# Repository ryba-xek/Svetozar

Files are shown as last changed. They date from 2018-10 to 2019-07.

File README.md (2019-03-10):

# Svetozar: an open-source e-vehicles peripherals controller

View this project on [CADLAB.io](https://cadlab.io/project/1290).

_Current project status_: in active development. Some features work, some don't.

## In a nutshell:

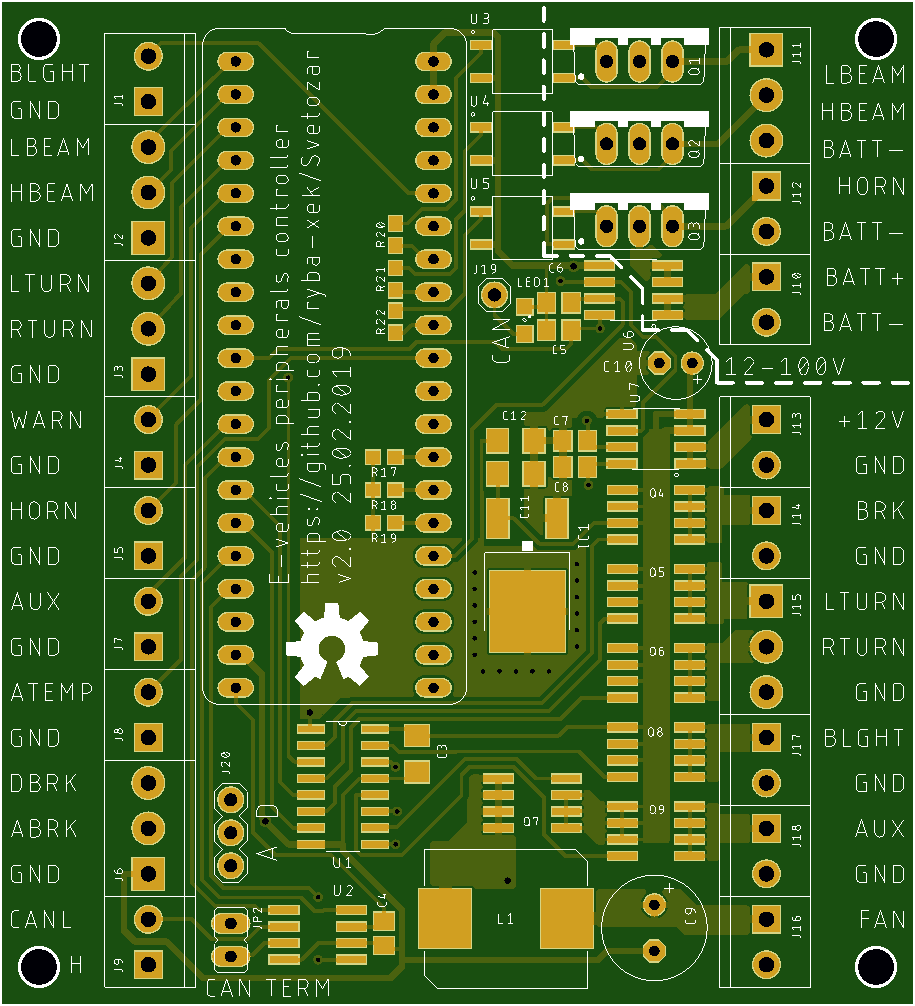
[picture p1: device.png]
device board


This ~30$ device allows you to control headlights/turn signals/horn/fan/etc on a typical e-bike/e-scooter.

It consists of a [‘Blue pill’](https://wiki.stm32duino.com/index.php?title=Blue_Pill) board with STM32F103 microcontroller which is widely available
on eBay or [Aliexpress](https://www.aliexpress.com/af/STM32F103C8T6.html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)
and a custom board with high-voltage circuitry. (You can order this board at [jlcpcb.com](https://jlcpcb.com/) for around 11$/10 pcs delivered.)

An external 12V power source is required. The device is able to switch 6x 12V outputs plus 3x 12..100V outputs
(12..100V nets are optically isolated). One of the 12V outputs is intended to drive a high-current fan and generates a stabilized 0..12V current
for a smooth fan speed control. CAN bus is also supported, so you can write some code to interact with other CAN devices.
There are 11 inputs on the left side, most of them are digital and trigger when connected to ground. ABRK input is analog and accepts voltages up to 5V,
ATEMP input should be used with KTY84/130 temperature sensor (or NTC10k, but you'll have to change input resistors to match the sensor).

## Current functions:

- Stoplight has medium brightness when not triggered
- ABRK & DBRK trigger stoplight to full brightness with a starting blink
- LTURN, RTURN, WARN trigger (left/right/both) turn signals flash with ~1 Hz frequency
- LBEAM triggers LBEAM output
- HBEAM triggers both LBEAM & HBEAM outputs
- HORN triggers HORN output
- AUX triggers AUX output
- BLGHT triggers BLGHT output
- ATEMP can be programmed to smoothly control FAN output
- 12V net triggers current protection at ~25A peak, this disables all 12V outputs 
- BATT+ net triggers current protection at ~12A peak, this disables all 12..100V outputs

## Hardware requirements

* Blue pill board
* Main board with all the components soldered ([BOM](bom.pdf))
* ST-Link/V2 or V2-1 programmer (V1 is supported via native ST software under Windows)

## Firmware requirements

* [Arduino IDE](https://www.arduino.cc/en/Main/Software)
* Arduino SAM boards (Cortex-M3) support installed from Ardiuno IDE's boards manager
* [coddingtonbear's fork](https://github.com/coddingtonbear/Arduino_STM32) of Arduino STM32 ‘hardware’ files with hardware CAN support (`HardwareCAN` git branch)
* [STM32duino bootloader](https://github.com/rogerclarkmelbourne/STM32duino-bootloader/raw/master/binaries/generic_boot20_pc13.bin) for Blue pill boards
* Some STM32 [ST-Link/V2](https://github.com/pavelrevak/pystlink) or [USB-TTL](https://www.st.com/content/st_com/en/products/development-tools/software-development-tools/stm32-software-development-tools/stm32-programmers/flasher-stm32.html) flashing software

## Flashing a Blue Pill board with the bootloader

### Mac OS X
#### Requirements
##### Software
* python 3.x (brew install python)
* libusb (brew reinstall libusb)
* pyusb (pip3 install pyusb)
* [pystlink](https://github.com/pavelrevak/pystlink)

#### Process
1. Download [STM32duino bootloader](https://github.com/rogerclarkmelbourne/STM32duino-bootloader/raw/master/binaries/generic_boot20_pc13.bin)
2. Connect ST-Link programmer to the board
3. Flash it with
```shell
    pystlink --cpu STM32F103xB flash:erase:verify:generic_boot20_pc13.bin
```
4. Reset or re-connect the board

### Windows
#### To Do

#### Flashing via USB-TTL adapter under Windows
[Please read this russian article](https://habr.com/post/395577/)

## Installing Arduino with STM32duino support
[STM32duino installation instructions](https://github.com/rogerclarkmelbourne/Arduino_STM32/wiki/Installation)

### Mac OS X
1. Install Arduino
2. Install libusb (brew install libusb)
3. Launch Arduino IDE, go to Tools -> Board: ... -> Boards Manager and install the Arduino SAM boards (Cortex-M3) support.
4. Download [coddingtonbear's fork](https://github.com/coddingtonbear/Arduino_STM32) of Arduino STM32 ‘hardware’ files
with hardware CAN support, checkout `HardwareCAN` branch and move and rename it to ```~/Documents/Arduino/hardware/Arduino_STM32```.
5. In Arduino IDE select Tools -> Board: ... -> Generic STM32F103C series.
5. In Arduino IDE select Tools -> CPU speed(MHz): -> 48MHz.

## Credits
Blue pill board library is from [github/sagarHackeD](https://github.com/sagarHackeD/STM32Bluepill_eagle)
VOM1271T.lbr, MAX3051ESA.lbr & MC14504BDR2G.lbr are from [SnapEDA](https://www.snapeda.com/)

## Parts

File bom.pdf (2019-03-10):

### bom

Parts | Value | MPN | Package | Qty | Description
C1, C2, C4, C5, C8 | 0.1u | CC0805KRX7R9BB104 | C0805 | 5 | CAPACITOR, European symbol
C10 | 220u | SK016M0220BZF-0611 | E2,5-6 | 1 | POLARIZED CAPACITOR, European symbol
C11 | 22u 16V | CL31A226KOHNNNE | C1206 | 1 | CAPACITOR, European symbol
C12 | 47u | CL31A476MQHNNNE | C1206 | 1 | CAPACITOR, European symbol
C3 | 0.1u | CC1206KRX7R8BB104 | C1206 | 1 | CAPACITOR, European symbol
C6, C7 | 1n | CL21B102KBANNNC | C0805 | 2 | CAPACITOR, European symbol
C9 | 470u | SK016M0470B3F-0811 | E3,5-8 | 1 | POLARIZED CAPACITOR, European symbol
D1, D2, D3, D4, D5 | | ES1D | DO214AC | 5 | DIODE
IC1 | | NCP1117DT33G | DPACK | 1 | Low drop fixed and adjustable positive voltage regulators 1 A
J1,J4,J5,J7,J8,J9,J10,J12,J13,J14,J16,J17,J18 | | DG350-3.5-02P-14-00AH | SCREWTERMINAL-3.5MM-2 | 13 | Screw terminal connector 3.5mm x 2
J11,J15,J2,J3,J6 | | DG350-3.5-03P-14-00AH | SCREWTERMINAL-3.5MM-3 | 5 | Screw terminal connector 3.5mm x 3
J19 | | PLS-1 | 1X01 | 1 | JUMPER
J20 | | PLS-3 | 1X03 | 1 | JUMPER
JP2 | | PLS-2 | JP1 | 1 | JUMPER
L1 | | SRP1040-150M | SRP1040 | 1 | POWER INDUCTOR
LED1 | | KPT-2012ZGC | SML0805 | 1 | LED, Vfd ~3.3V
Q1, Q2, Q3 | | PHP20NQ20T.127 | TO220BV | 3 | Power MOSFET N-Channel
Q4, Q5, Q6, Q7, Q8, Q9 | | IRF7424TRPBF | SO-08 | 6 | P-Channel MOSFET
R1, R2, R3, R4, R5, R6, R7, R8, R11 | 1K | RC0603JR-071KL | 0603 | 9 | Resistor
R12 | 2.4K | RC0603FR-072K4L | 0603 | 1 | Resistor
R13 | 120 | RC0603FR-07120RL | 0603 | 1 | Resistor
R10,R14, R15, R16, R17, R18, R19 | 10K | RC0603JR-0710KL | 0603 | 7 | Resistor
R20, R21, R22 | 160 | RC0805FR-07160RL | 0603 | 3 | Resistor
R9 | 3K | RC0603JR-073KL | 0603 | 1 | Resistor
U$1 | | PBS-20 | 1X20 | 2 | 20-pin header connector
U1 | | MC14504BDR2G | SOIC−16 | 1 | Hex Level Shifter for TTL to CMOS or CMOS to CMOS
U2 | | MAX3051ESA+T | SO-08 | 1 | Can bus transciever
U3, U4, U5 | | VOM1271T | SOP-4 | 3 | Photovoltaic optocoupler
U6 | | ACS711KLCTR-12AB-T | SO-08 | 1 | Hall effect current sensor
U7 | | ACS711ELCTR-25AB-T | SO-08 | 1 | Hall effect current sensor

1

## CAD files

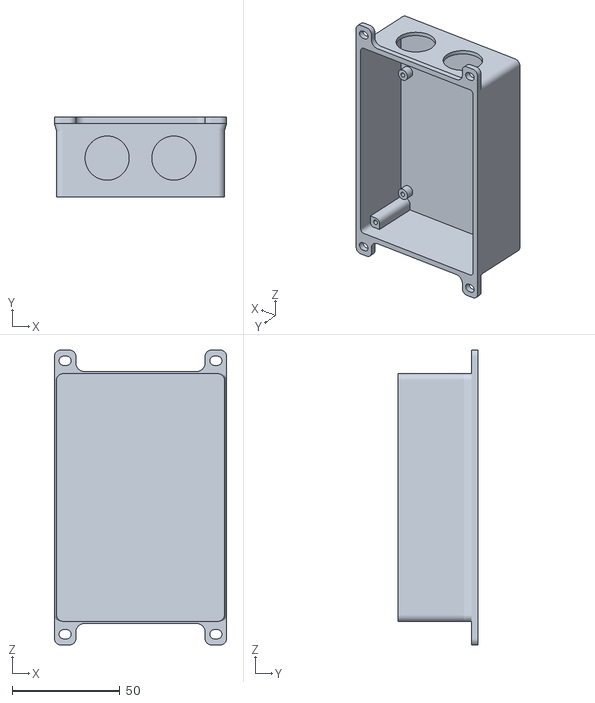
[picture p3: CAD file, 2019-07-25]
3d parts/Body.stl
80.0 x 37.0 x 137.0

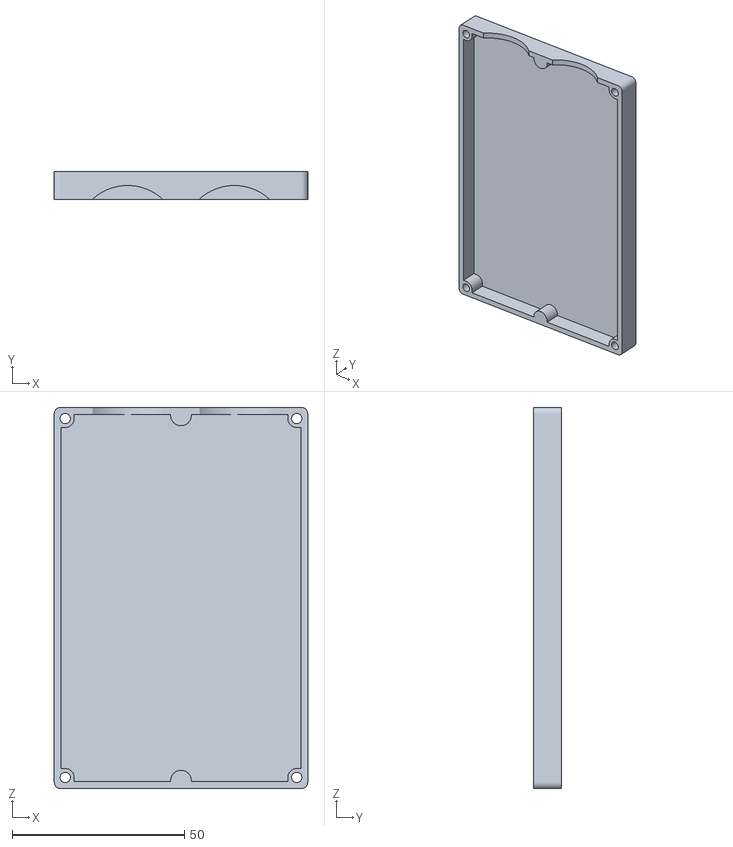
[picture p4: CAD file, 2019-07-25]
3d parts/Cover.stl
73.6 x 8.00 x 110.6

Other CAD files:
3d parts/box.f3d

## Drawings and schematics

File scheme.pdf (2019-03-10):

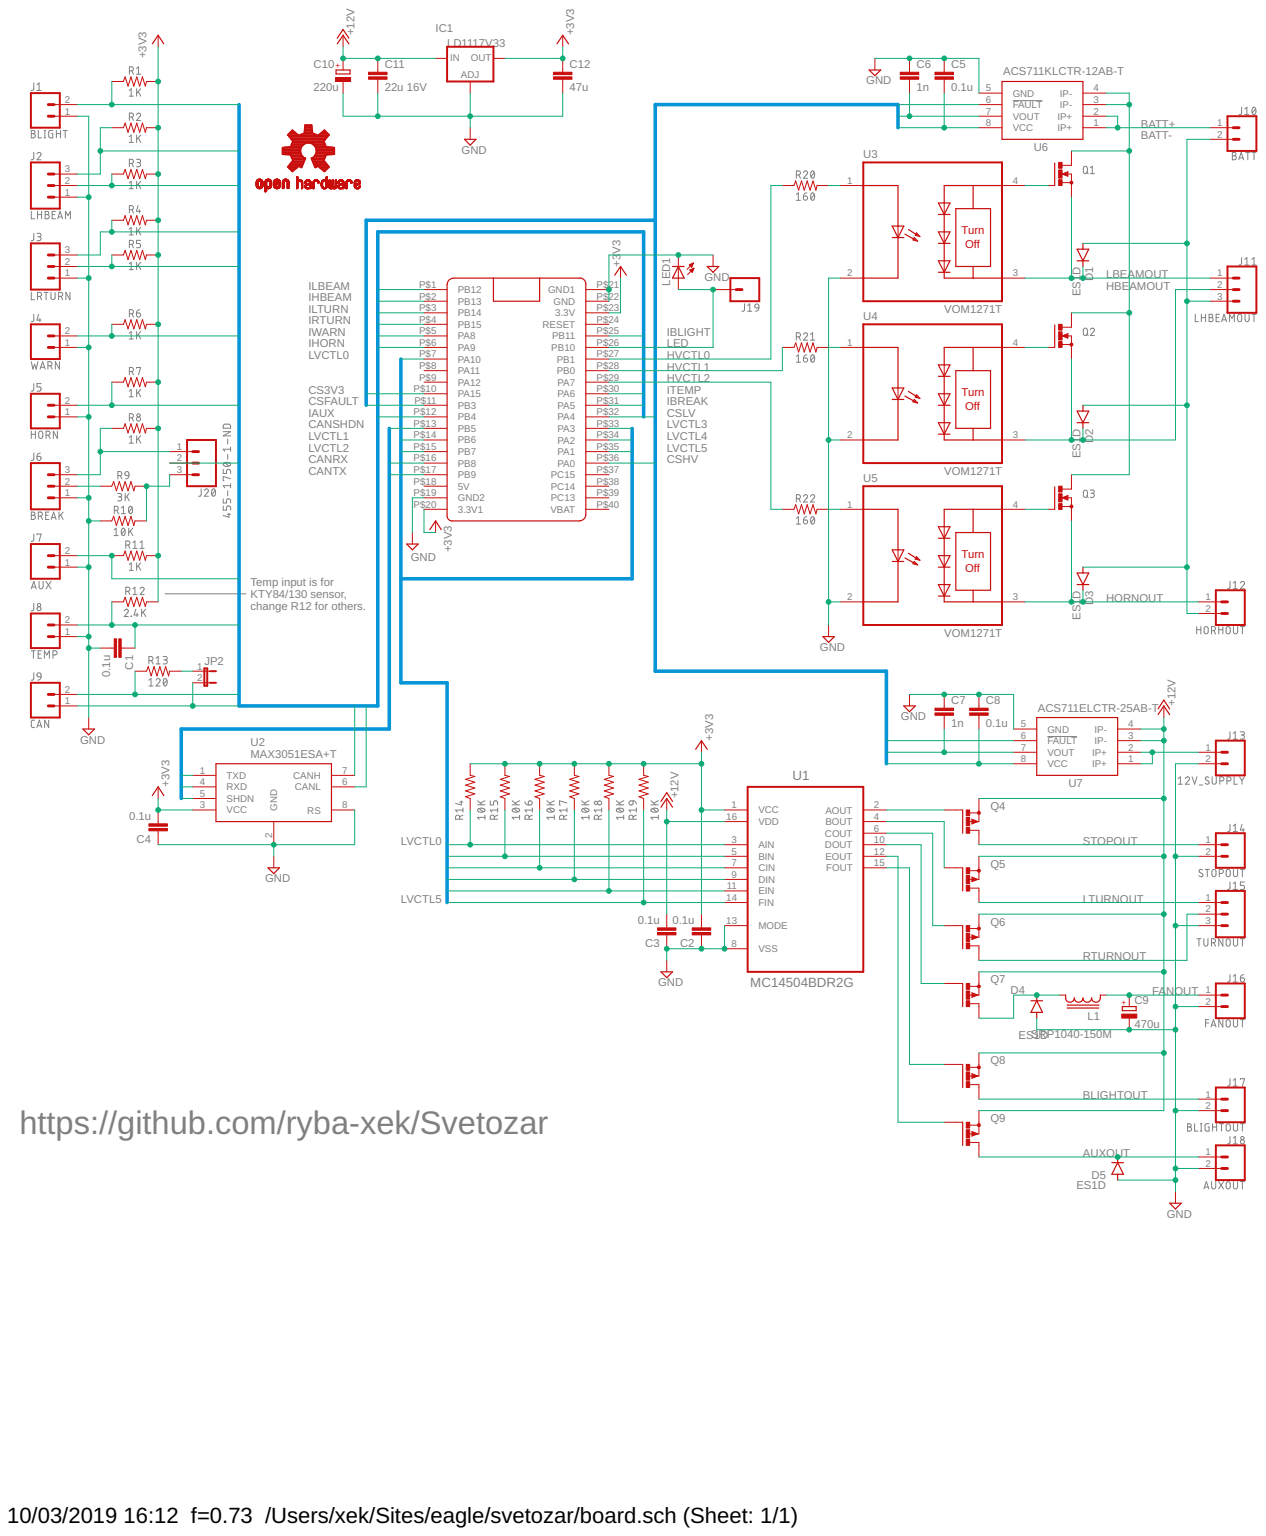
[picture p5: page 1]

Temp input is for KTY84/130 sensor, change R12 for others.

https://github.com/ryba-xek/Svetozar

10/03/2019 16:12 f=0.73 /Users/xek/Sites/eagle/svetozar/board.sch (Sheet: 1/1)

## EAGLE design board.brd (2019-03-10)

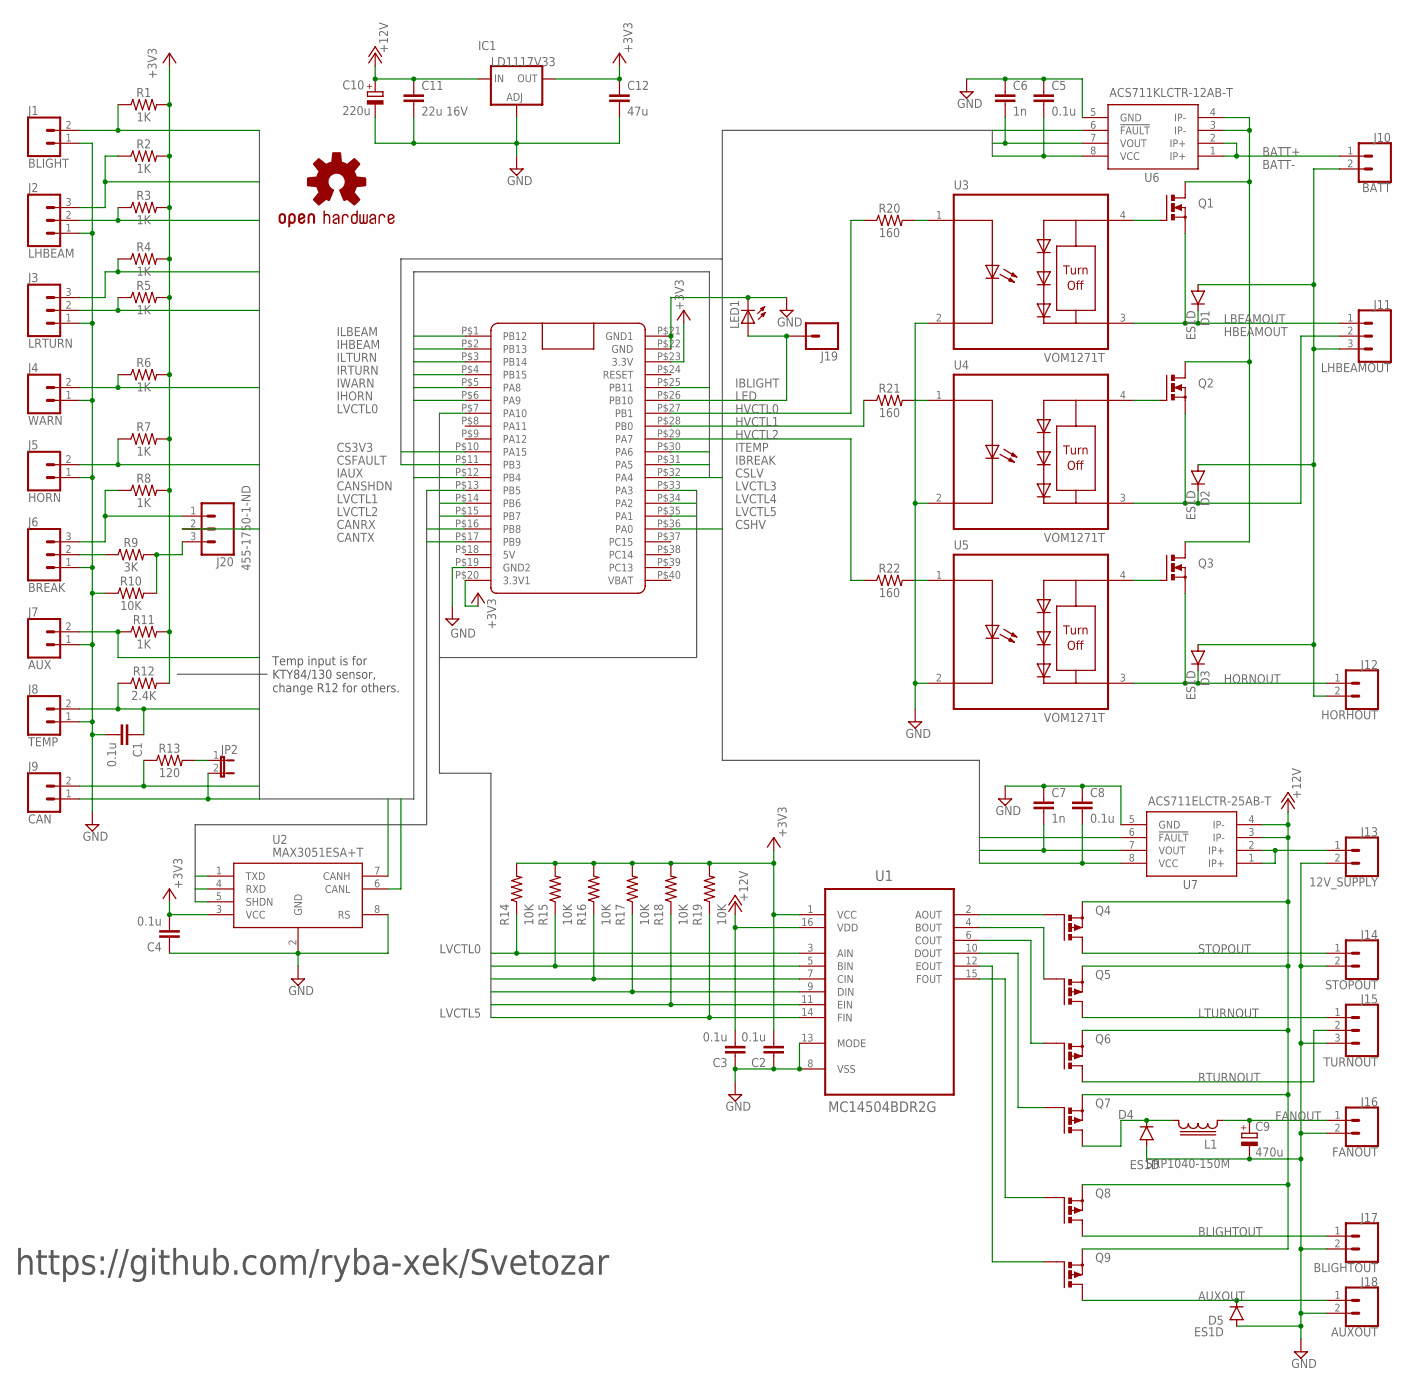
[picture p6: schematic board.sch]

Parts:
C1, C2, C4, C5, C8: 0.1u; C0805; MPN CC0805KRX7R9BB104
C3: 0.1u; C1206; MPN CC1206KRX7R8BB104
C6, C7: 1n; C0805; MPN CL21B102KBANNNC
C9: 470u; E3,5-8; MPN SK016M0470B3F-0811
C10: 220u; E2,5-6; MPN SK016M0220BZF-0611
C11: 22u 16V; C1206; MPN CL31A226KOHNNNE
C12: 47u; C1206; MPN CL31A476MQHNNNE
D1, D2, D3, D4, D5: ES1D; DO214AC; MPN ES1D
IC1: LD1117V33; DPACK; MPN NCP1117DT33G
J1: BLIGHT; SCREWTERMINAL-3.5MM-2; MPN DG350-3.5-02P-14-00AH
J2: LHBEAM; SCREWTERMINAL-3.5MM-3; MPN DG350-3.5-03P-14-00AH
J3: LRTURN; SCREWTERMINAL-3.5MM-3; MPN DG350-3.5-03P-14-00AH
J4: WARN; SCREWTERMINAL-3.5MM-2; MPN DG350-3.5-02P-14-00AH
J5: HORN; SCREWTERMINAL-3.5MM-2; MPN DG350-3.5-02P-14-00AH
J6: BREAK; SCREWTERMINAL-3.5MM-3; MPN DG350-3.5-03P-14-00AH
J7: AUX; SCREWTERMINAL-3.5MM-2; MPN DG350-3.5-02P-14-00AH
J8: TEMP; SCREWTERMINAL-3.5MM-2; MPN DG350-3.5-02P-14-00AH
J9: CAN; SCREWTERMINAL-3.5MM-2; MPN DG350-3.5-02P-14-00AH
J10: BATT; SCREWTERMINAL-3.5MM-2; MPN DG350-3.5-02P-14-00AH
J11: LHBEAMOUT; SCREWTERMINAL-3.5MM-3; MPN DG350-3.5-03P-14-00AH
J12: HORHOUT; SCREWTERMINAL-3.5MM-2; MPN DG350-3.5-02P-14-00AH
J13: 12V_SUPPLY; SCREWTERMINAL-3.5MM-2; MPN DG350-3.5-02P-14-00AH
J14: STOPOUT; SCREWTERMINAL-3.5MM-2; MPN DG350-3.5-02P-14-00AH
J15: TURNOUT; SCREWTERMINAL-3.5MM-3; MPN DG350-3.5-03P-14-00AH
J16: FANOUT; SCREWTERMINAL-3.5MM-2; MPN DG350-3.5-02P-14-00AH
J17: BLIGHTOUT; SCREWTERMINAL-3.5MM-2; MPN DG350-3.5-02P-14-00AH
J18: AUXOUT; SCREWTERMINAL-3.5MM-2; MPN DG350-3.5-02P-14-00AH
J19: CONN_01; 1X01; MPN PLS-1
J20: 455-1750-1-ND; 1X03; MPN PLS-3
JP2: JP1E; JP1; MPN PLS-2
L1: SRP1040-150M; SRP1040; MPN SRP1040-150M
LED1: LEDSML0805; SML0805; MPN KPT-2012ZGC
LOGO1: OSHW-LOGOL; OSHW-LOGO-L
Q1, Q2, Q3: PHP20NQ20T; TO220BV; MPN PHP20NQ20T.127
Q4, Q5, Q6, Q7, Q8, Q9: P-MOSFET-SO8; SO-08; MPN IRF7424TRPBF
R1, R2, R3, R4, R5, R6, R7, R8, R11: 1K; 0603; MPN RC0603JR-071KL
R9: 3K; 0603; MPN RC0603JR-073KL
R10, R14, R15, R16, R17, R18, R19: 10K; 0603; MPN RC0603JR-0710KL
R12: 2.4K; 0603; MPN RC0603FR-072K4L
R13: 120; 0603; MPN RC0603FR-07120RL
R20, R21, R22: 160; 0603; MPN RC0603FR-07160RL
U1: MC14504BDR2G; SOIC127P600X175-16N; MPN MC14504BDR2G
U2: MAX3051ESA+T; SO-08; MPN MAX3051ESA+T
U3, U4, U5: VOM1271T; SOIC254P695X242-4N; MPN VOM1271T
U6: ACS711KLCTR-12AB-T; SO08; MPN ACS711KLCTR-12AB-T
U7: ACS711ELCTR-25AB-T; SO08; MPN ACS711ELCTR-25AB-T
U$1: BLUE_PILL

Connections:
12V_IN: J13.1, U7.1 (IP+), U7.2 (IP+)
+3V3: C2.2, C4.2, C12.1, IC1.4 (OUT), R1.2, R2.2, R3.2, R4.2, R5.2, R6.2, R7.2, R8.2, R11.2, R12.2, R14.2, R15.2, R16.2, R17.2, R18.2, R19.2, U1.1 (VCC), U2.3 (VCC), U$1.P$20 (3.3V1), U$1.P$23 (3.3V)
+12V: C3.2, C10.+, C11.1, IC1.3 (IN), Q4.1 (S), Q4.2 (S), Q4.3 (S), Q5.1 (S), Q5.2 (S), Q5.3 (S), Q6.1 (S), Q6.2 (S), Q6.3 (S), Q7.1 (S), Q7.2 (S), Q7.3 (S), Q8.1 (S), Q8.2 (S), Q8.3 (S), Q9.1 (S), Q9.2 (S), Q9.3 (S), U1.16 (VDD), U7.3 (IP-), U7.4 (IP-)
AUXOUT: D5.C, J18.1, Q9.5 (D), Q9.6 (D), Q9.7 (D), Q9.8 (D)
BATT+: J10.1, U6.1 (IP+), U6.2 (IP+)
BATT-: D1.A, D2.A, D3.A, J10.2, J11.3, J12.2
BLIGHTOUT: J17.1, Q8.5 (D), Q8.6 (D), Q8.7 (D), Q8.8 (D)
CANH: J9.1, JP2.2, U2.7 (CANH)
CANL: J9.2, R13.1, U2.6 (CANL)
CANRX: U2.4 (RXD), U$1.P$16 (PB8)
CANSHDN: U2.5 (SHDN), U$1.P$13 (PB5)
CANTX: U2.1 (TXD), U$1.P$17 (PB9)
CS3V3: C5.2, C8.2, U6.8 (VCC), U7.8 (VCC), U$1.P$10 (PA15)
CSFAULT: U6.6 (!FAULT), U7.6 (!FAULT), U$1.P$11 (PB3)
CSHV: C6.2, U6.7 (VOUT), U$1.P$36 (PA0)
CSLV: C7.2, U7.7 (VOUT), U$1.P$32 (PA4)
FANOUT: C9.+, J16.1, L1.1
FANPWM: D4.C, L1.2, Q7.5 (D), Q7.6 (D), Q7.7 (D), Q7.8 (D)
GND: C1.2, C2.1, C3.1, C4.1, C5.1, C6.1, C7.1, C8.1, C9.-, C10.-, C11.2, C12.2, D4.A, D5.A, IC1.1 (ADJ), J1.1, J2.1, J3.1, J4.1, J5.1, J6.1, J7.1, J8.1, J13.2, J14.2, J15.3, J16.2, J17.2, J18.2, LED1.C, R10.1, U1.8 (VSS), U1.13 (MODE), U2.2 (GND), U2.8 (RS), U3.2 (C1), U4.2 (C1), U5.2 (C1), U6.5 (GND), U7.5 (GND), U$1.P$19 (GND2), U$1.P$21 (GND1), U$1.P$22 (GND)
HBEAMOUT: D2.C, J11.2, Q2.S, U4.3 (C2)
HORNOUT: D3.C, J12.1, Q3.S, U5.3 (C2)
HV: Q1.D, Q2.D, Q3.D, U6.3 (IP-), U6.4 (IP-)
HVCTL0: R20.1, U$1.P$27 (PB1)
HVCTL1: R21.1, U$1.P$28 (PB0)
HVCTL2: R22.1, U$1.P$29 (PA7)
IAUX: J7.2, R11.1, U$1.P$12 (PB4)
IBLIGHT: J1.2, R1.1, U$1.P$25 (PB11)
IBREAK: J20.2, U$1.P$31 (PA5)
IHBEAM: J2.2, R3.1, U$1.P$2 (PB13)
IHORN: J5.2, R7.1, U$1.P$6 (PA9)
ILBEAM: J2.3, R2.1, U$1.P$1 (PB12)
ILTURN: J3.3, R4.1, U$1.P$3 (PB14)
IRTURN: J3.2, R5.1, U$1.P$4 (PB15)
ITEMP: C1.1, J8.2, R12.1, U$1.P$30 (PA6)
IWARN: J4.2, R6.1, U$1.P$5 (PA8)
LBEAMOUT: D1.C, J11.1, Q1.S, U3.3 (C2)
LED: J19.1, LED1.A, U$1.P$26 (PB10)
LTURNOUT: J15.1, Q5.5 (D), Q5.6 (D), Q5.7 (D), Q5.8 (D)
LVCTL0: R14.1, U1.3 (AIN), U$1.P$7 (PA10)
LVCTL1: R15.1, U1.5 (BIN), U$1.P$14 (PB6)
LVCTL2: R16.1, U1.7 (CIN), U$1.P$15 (PB7)
LVCTL3: R17.1, U1.9 (DIN), U$1.P$33 (PA3)
LVCTL4: R18.1, U1.11 (EIN), U$1.P$34 (PA2)
LVCTL5: R19.1, U1.14 (FIN), U$1.P$35 (PA1)
LVG0: Q4.4 (G), U1.2 (AOUT)
LVG1: Q5.4 (G), U1.4 (BOUT)
LVG2: Q6.4 (G), U1.6 (COUT)
LVG3: Q7.4 (G), U1.10 (DOUT)
LVG4: Q8.4 (G), U1.15 (FOUT)
LVG5: Q9.4 (G), U1.12 (EOUT)
unnamed: J6.3, J20.1, R8.1
unnamed: JP2.1, R13.2
unnamed: J20.3, R9.2, R10.2
unnamed: J6.2, R9.1
unnamed: R20.2, U3.1 (A1)
unnamed: Q1.G, U3.4 (A2)
unnamed: R21.2, U4.1 (A1)
unnamed: Q2.G, U4.4 (A2)
unnamed: R22.2, U5.1 (A1)
unnamed: Q3.G, U5.4 (A2)
RTURNOUT: J15.2, Q6.5 (D), Q6.6 (D), Q6.7 (D), Q6.8 (D)
STOPOUT: J14.1, Q4.5 (D), Q4.6 (D), Q4.7 (D), Q4.8 (D)

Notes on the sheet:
https://github.com/ryba-xek/Svetozar
Temp input is for KTY84/130 sensor, change R12 for others.

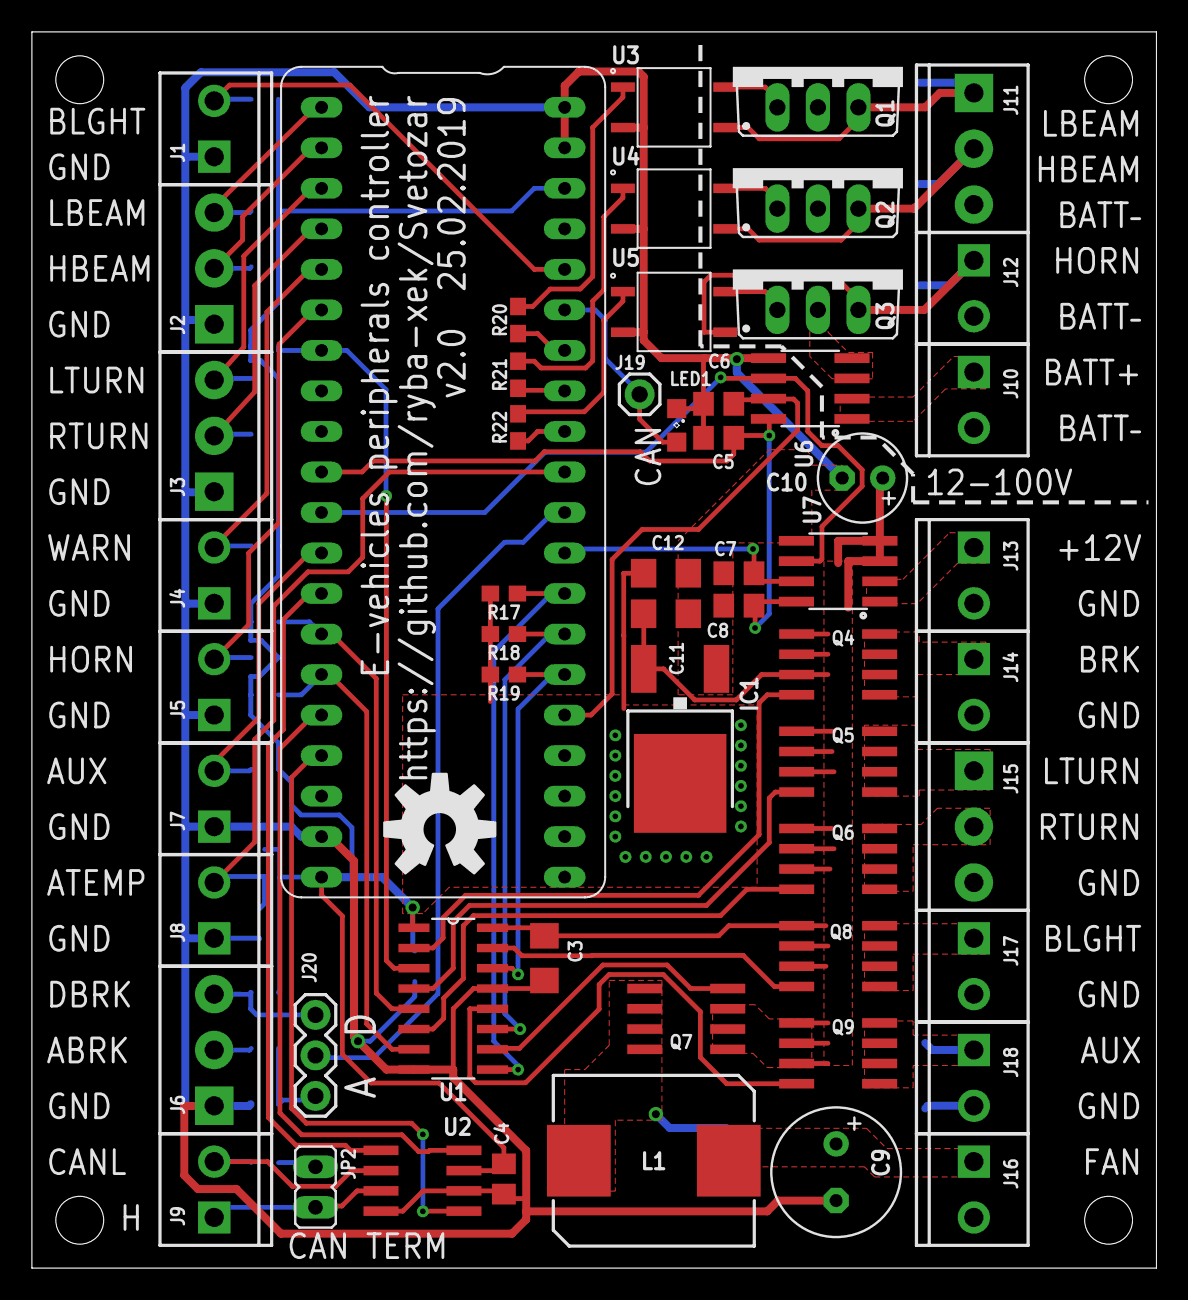
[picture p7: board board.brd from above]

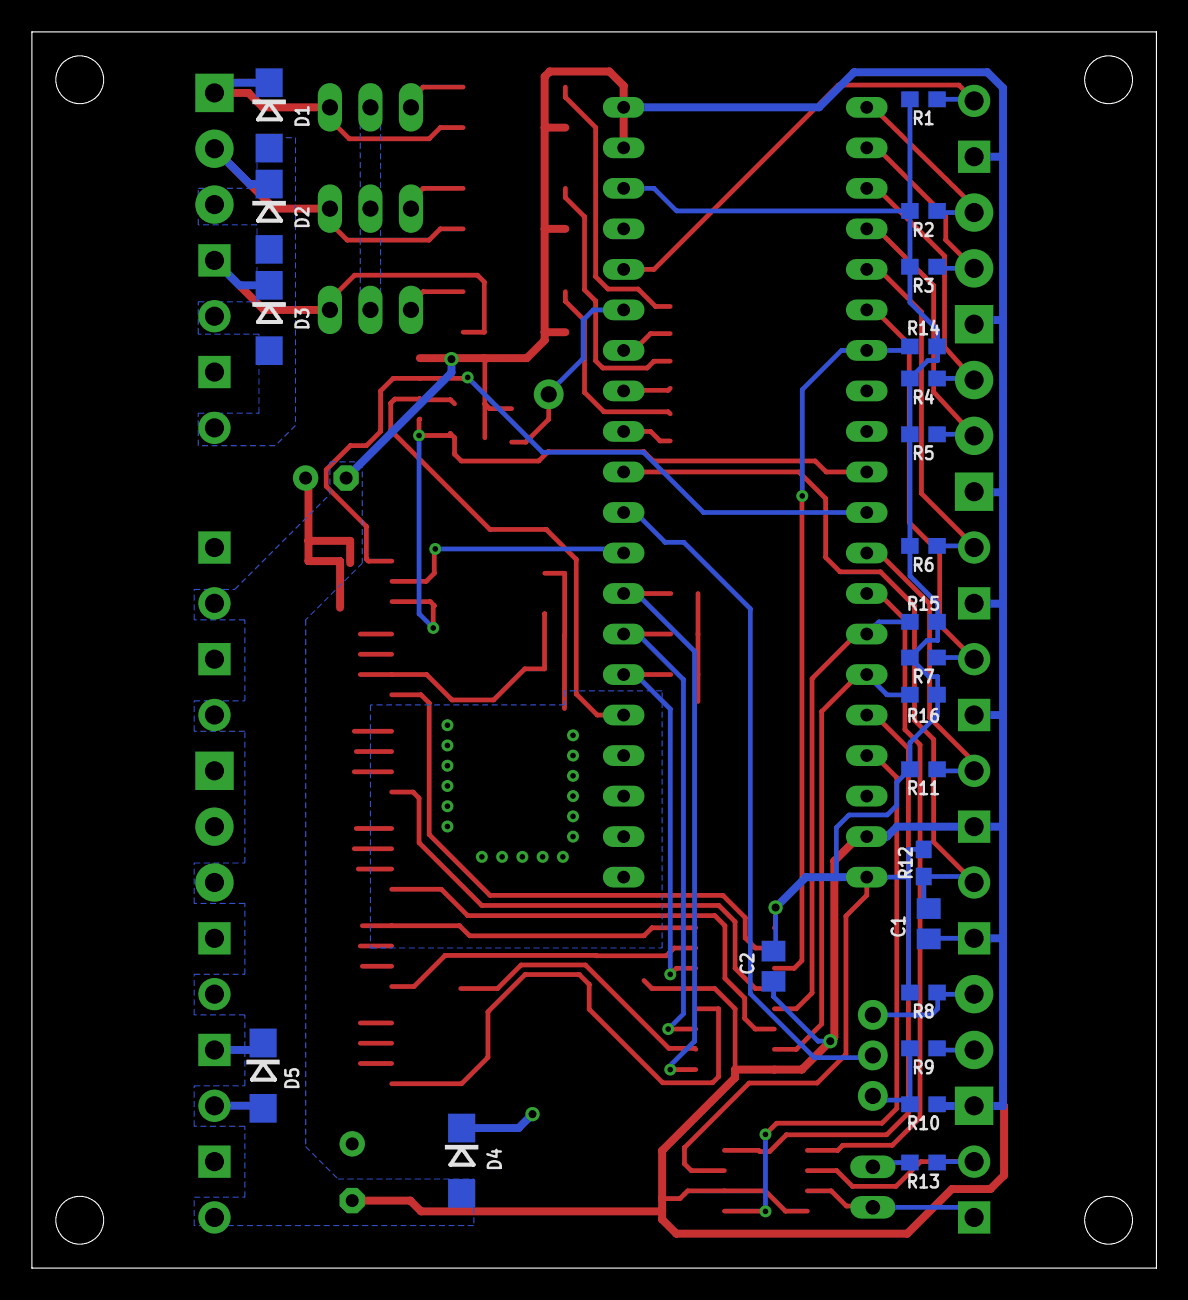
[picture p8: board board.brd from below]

Board: 2 copper layers, 70.5 x 77.5 mm, 81 parts (23 on the bottom side), 62 nets.

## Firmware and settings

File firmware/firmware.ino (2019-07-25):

#include "can.h"
#include "config.h"
#include "board.h"
#include "HardwareSerial.h"
#include <HardwareCAN.h>

/*
 * Svetozar: an open-source e-vehicles peripherals controller
 * Supported board version: v1.2
 *
 * TODO:
 *  - analog temp sensor
 *
 * NOTES:
 *   - switch CPU frequency to 48 MHz
 *   - edit config.h
 *   - do not use delay() function
 */

bool csfault = false; //overcurrent shutdown
bool blightOn = false;
bool hbeamOn = false;
bool lbeamOn = false;
bool rturnOn = false;
bool lturnOn = false;
bool warnOn = false;
bool hornOn = false;
bool breakOn = false;
bool auxOn = false;
uint8 motorTemp = 0;
uint16 fanValue = 0;

bool routinesRunning;
bool needQueryTemp = false;
uint breakCtr = 0;
uint turnCtr = 0;


void csFaultTriggered() {
    csfault = true;
    pinMode(STOP_OUT_PIN,        OUTPUT);
    digitalWrite(STOP_OUT_PIN,   HIGH); //off
    pinMode(BLIGHT_OUT_PIN,      OUTPUT);
    digitalWrite(BLIGHT_OUT_PIN, HIGH); //off
    pinMode(FAN_OUT_PIN,         OUTPUT);
    digitalWrite(FAN_OUT_PIN,    HIGH); //off
    pinMode(AUX_OUT_PIN,         OUTPUT);
    digitalWrite(AUX_OUT_PIN,    HIGH); //off
    digitalWrite(LTURN_OUT_PIN,  HIGH); //off
    digitalWrite(RTURN_OUT_PIN,  HIGH); //off
    digitalWrite(HBEAM_OUT_PIN,  LOW);  //off
    digitalWrite(LBEAM_OUT_PIN,  LOW);  //off
    digitalWrite(HORN_OUT_PIN,   LOW);  //off
}

void readInPins() {
    // update input vars
    blightOn = digitalRead(BLIGHT_IN_PIN) == LOW;
    hbeamOn  = digitalRead(HBEAM_IN_PIN)  == LOW;
    lbeamOn  = digitalRead(LBEAM_IN_PIN)  == LOW;
    rturnOn  = digitalRead(RTURN_IN_PIN)  == LOW;
    lturnOn  = digitalRead(LTURN_IN_PIN)  == LOW;
    warnOn   = digitalRead(WARN_IN_PIN)   == LOW;
    hornOn   = digitalRead(HORN_IN_PIN)   == LOW;
    breakOn  = digitalRead(BREAK_IN_PIN)  == LOW;
    auxOn    = digitalRead(AUX_IN_PIN)    == LOW;

//    #if USE_ANALOG_STOP
        //breakOn = breakOn || (analogRead(ABREAK_IN_PIN) < STOP_ANALOG_THRESHOLD);
//    #endif
}

void processPeriodicTask() { // called every 50 ms
    uint16 stopLightValue;
    bool   turnLightsValue;

    // update input data
    readInPins();  // sometimes EXTi interrupt is not fired, this helps
    needQueryTemp = true;

    // light up led if any input is triggered
    digitalWrite(LED_OUT_PIN, !(blightOn || hbeamOn || lbeamOn || rturnOn || lturnOn || warnOn || hornOn || breakOn || auxOn));

    // LED2
    if (csfault) {
        digitalWrite(LED2_OUT_PIN, !digitalRead(LED2_OUT_PIN));
        return;
    } else {
        digitalWrite(LED2_OUT_PIN, LOW);
    }
    
    // stoplight
    if (!breakOn) {
        breakCtr = 0;
        stopLightValue = STOP_HALF_VALUE;
    } else {
        stopLightValue = (breakCtr / STOP_BLINK_TIME) % 2 == 0 ? STOP_ON_VALUE : 0;
        breakCtr = min(STOP_BLINK_TIME * STOP_BLINK_NUM * 2, breakCtr+1);
    }
    pwmWrite(STOP_OUT_PIN, stopLightValue);

    // turn signals
    if (!(lturnOn || rturnOn || warnOn)) {
        turnCtr = 0;
        turnLightsValue = false;
    } else {
        turnLightsValue = turnCtr < TURN_BLINK_PERIOD/2; // 0,1,2,3,4 - on, 5,6,7,8,9 - off
        turnCtr++; //TODO: move to interrupt handler
        if (turnCtr == TURN_BLINK_PERIOD) turnCtr = 0;
    }
    digitalWrite(LTURN_OUT_PIN, !(turnLightsValue && (lturnOn || warnOn)));
    digitalWrite(RTURN_OUT_PIN, !(turnLightsValue && (rturnOn || warnOn)));

    // high beam, low beam, horn
    digitalWrite(HBEAM_OUT_PIN, hbeamOn);
    digitalWrite(LBEAM_OUT_PIN, lbeamOn || hbeamOn);
    digitalWrite(HORN_OUT_PIN,  hornOn);

    // backlight, aux
    //pwmWrite(BLIGHT_OUT_PIN, blightOn ? BLIGHT_ON_VALUE : 0);
    pwmWrite(AUX_OUT_PIN, auxOn ? AUX_ON_VALUE : 0);

    // fan
    fanValue = min(fanValue+5, FAN_MAX_VALUE);
    if (!lbeamOn) fanValue = 0;
    pwmWrite(FAN_OUT_PIN, fanValue); //calcFanPwm(motorTemp) // blightOn ? 1024 : 0
    
    char buffer[100];
    uint16 v;
    v = calcFanPwm(motorTemp);
    sprintf(buffer, "debug: %d", v);
    //Serial3.println(buffer);
     
//    Serial3.print("Motor temp: ");
//    Serial3.print(motorTemp);
//    Serial3.print(", fan PWM value: ");
//    Serial3.println(calcFanPwm(motorTemp));

    // can CPU sleep?
    routinesRunning = breakOn || lturnOn || rturnOn || warnOn;

    //pass control to loop()
}

void setup() {
    #if CAN_BUS_ENABLED
        // CAN conflicts with USB, disable USB
        #ifdef SERIAL_USB
            Serial.end();
        #endif

      CANSetup();  // Initialize the CAN module and prepare the message structures
    #endif
    
    BoardSetup(readInPins, csFaultTriggered);
    
    systick_attach_callback(processPeriodicTask);
    //Serial3.print("Setup over");
}

uint16 calcFanPwm(uint8 temp) {
    if (temp < MOTOR_TRIGGER_TEMP) {
        return 0;
    }

    if (temp >= MOTOR_MAX_TEMP) {
        return FAN_MAX_VALUE;
    }

    return FAN_MIN_VALUE + (temp - MOTOR_TRIGGER_TEMP) * (FAN_MAX_VALUE - FAN_MIN_VALUE) / (MOTOR_MAX_TEMP - MOTOR_TRIGGER_TEMP);
}

void loop() {
    CanMsg *r_msg;
    float temp;

    #if CAN_BUS_ENABLED
        if (needQueryTemp) {
            needQueryTemp = false;
            SendCANmessage(CAN_MOTOR_TEMP_REQ_MSGID, 8, 0x40, 0x08, 0x21, 0x2, 0x0, 0x0, 0x0, 0x0);
        }
    #endif

    #if CAN_BUS_ENABLED
    // process CAN messages
    while ((r_msg = canBus.recv()) != NULL) {
        switch (r_msg->ID) {
            case CAN_BREAK_MSGID:
                breakOn |= bitRead(r_msg->Data[6], 1);
                break;

            case CAN_MOTOR_TEMP_MSGID:
                char tempbytes[4] = {r_msg->Data[4], r_msg->Data[5], r_msg->Data[6], r_msg->Data[7]};
                memcpy(&temp, tempbytes, sizeof(float));
                motorTemp = temp;
                break;

            default:
                break;
        }

        canBus.free();
    }
    #endif

    // sleep when no turn/stop lights are on
    if (!routinesRunning) {
        asm("wfi");
    }
}

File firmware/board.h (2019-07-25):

/*
 * Svetozar: an open-source e-vehicles peripherals controller
 * Supported board version: v1.1
 *
 *
 * Pin assignments:
 *                               _________________
 *                              /       L__J      \
 *                Low beam in - | PB12        GND | -
 *               High beam in - | PB13        GND | -
 *               Left turn in - | PB14       3.3V | -
 *              Right turn in - | PB15      RESET | -
 *                 Warning in - | PA8        PB11 | - Backlight in
 *                    Horn in - | PA9        PB10 | - USART TX3 & LED
 * TIM1_CH3     Stoplight out - | PA10        PB1 | - Low beam out            TIM3_CH4
 *                       USB- - | PA11        PB0 | - High beam out           TIM3_CH3
 *                       USB+ - | PA12        PA7 | - Horn out                TIM3_CH2
 *                ACS711LC V+ - | PA15        PA6 | - Analog temp sensor in
 *             Overcurrent in - | PB3         PA5 | - A/D break in
 *                     Aux in - | PB4         PA4 | - LV current sense
 *            CAN IC shutdown - | PB5         PA3 | - Fan out                 TIM2_CH4
 * TIM4_CH1    Right turn out - | PB6         PA2 | - Backlight out           TIM2_CH3
 * TIM4_CH2     Left turn out - | PB7         PA1 | - Aux out                 TIM2_CH2
 *                     CAN Rx - | PB8         PA0 | - HV current sense
 *                     CAN Tx - | PB9        PC15 | - LSE oscillator in
 *                            - | 5V         PC14 | - LSE oscillator out
 *                            - | GND        PC13 | - Onboard LED out
 *                            - | 3.3V       VBAT |
 *                              \_________________/
 *
 * EXTi map:
 * EXTI0:
 * EXTI1:
 * EXTI2:
 * EXTI3: PB3 - Overcurrent in
 * EXTI4: PB4 - Aux in
 * EXTI5: PA5 - Break in
 * EXTI6:
 * EXTI7:
 * EXTI8: PA8 - Warning in
 * EXTI9: PA9 - Horn in
 * EXTI10:
 * EXTI11: PB11 - Backlight in
 * EXTI12: PB12 - Low beam in
 * EXTI13: PB13 - High beam in
 * EXTI14: PB14 - Left turn in
 * EXTI15: PB15 - Right turn in
 */


#ifndef BOARD_H
#define BOARD_H

#if F_CPU != 48000000UL
    #error "Please select Tools -> CPU Speed -> 48Mhz"
#endif


#define LBEAM_IN_PIN    PB12
#define HBEAM_IN_PIN    PB13
#define LTURN_IN_PIN    PB14
#define RTURN_IN_PIN    PB15
#define WARN_IN_PIN     PA8
#define HORN_IN_PIN     PA9
#define STOP_OUT_PIN    PA10
#define CSSUPPLY_PIN    PA15
#define CSFAULT_IN_PIN  PB3
#define AUX_IN_PIN      PB4
#define CAN_SHDN_PIN    PB5
#define RTURN_OUT_PIN   PB6
#define LTURN_OUT_PIN   PB7
#define CAN_RX_PIN      PB8
#define CAN_TX_PIN      PB9

#define BLIGHT_IN_PIN   PB11
#define LED2_OUT_PIN    PB10
#define LBEAM_OUT_PIN   PB1
#define HBEAM_OUT_PIN   PB0
#define HORN_OUT_PIN    PA7
#define ATEMP_IN_PIN    PA6
#define BREAK_IN_PIN    PA5
#define LVCS_IN_PIN     PA4
#define FAN_OUT_PIN     PA3
#define BLIGHT_OUT_PIN  PA2
#define AUX_OUT_PIN     PA1
#define HVCS_IN_PIN     PA0
#define LED_OUT_PIN     PC13

void BoardSetup(void (*callback)(void), void (*csFaultCallback)(void));

#endif //BOARD_H

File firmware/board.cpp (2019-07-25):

#include "Arduino.h"
#include "board.h"
#include "config.h"

// PWM timers
HardwareTimer htimer1(1);
HardwareTimer htimer2(2);
HardwareTimer htimer3(3);
HardwareTimer htimer4(4);

void setPolarity(uint8 pin, uint8 pol) {
    if (pin >= BOARD_NR_GPIO_PINS) {
        return;
    }
    timer_dev *dev = PIN_MAP[pin].timer_device;
    uint8 cc_channel = PIN_MAP[pin].timer_channel;
    ASSERT(dev && cc_channel);
    timer_cc_set_pol(dev, cc_channel, pol);
}

void BoardSetup(void (*callback)(void), void (*csFaultCallback)(void)) {

    // Inputs
    pinMode(BLIGHT_IN_PIN,  INPUT);
    pinMode(HBEAM_IN_PIN,   INPUT);
    pinMode(LBEAM_IN_PIN,   INPUT);
    pinMode(RTURN_IN_PIN,   INPUT);
    pinMode(LTURN_IN_PIN,   INPUT);
    pinMode(WARN_IN_PIN,    INPUT);
    pinMode(HORN_IN_PIN,    INPUT);
    pinMode(BREAK_IN_PIN,   INPUT);
    pinMode(CSFAULT_IN_PIN, INPUT_PULLUP);
    pinMode(AUX_IN_PIN,     INPUT);
    pinMode(ATEMP_IN_PIN,   INPUT_ANALOG);
    pinMode(LVCS_IN_PIN,    INPUT_ANALOG);
    pinMode(HVCS_IN_PIN,    INPUT_ANALOG);

    // Digital outputs
    pinMode(CSSUPPLY_PIN,   OUTPUT);
    pinMode(LED_OUT_PIN,    OUTPUT);
    pinMode(LED2_OUT_PIN,   OUTPUT);
    pinMode(CAN_SHDN_PIN,   OUTPUT);
    pinMode(LTURN_OUT_PIN,  OUTPUT);
    pinMode(RTURN_OUT_PIN,  OUTPUT);
    pinMode(HBEAM_OUT_PIN,  OUTPUT);
    pinMode(LBEAM_OUT_PIN,  OUTPUT);
    pinMode(HORN_OUT_PIN,   OUTPUT);

    digitalWrite(CSSUPPLY_PIN,    HIGH);  // CS supply on
    digitalWrite(LED_OUT_PIN,    HIGH);  // LED off
    digitalWrite(CAN_SHDN_PIN,   !CAN_BUS_ENABLED);
    digitalWrite(LTURN_OUT_PIN,  HIGH);  // off
    digitalWrite(RTURN_OUT_PIN,  HIGH);  // off
    digitalWrite(HBEAM_OUT_PIN,  LOW);  // off
    digitalWrite(LBEAM_OUT_PIN,  LOW);  // off
    digitalWrite(HORN_OUT_PIN,   LOW);  // off
    
    // PWM outputs
    pinMode(STOP_OUT_PIN,   PWM);
    pinMode(BLIGHT_OUT_PIN, PWM);
    pinMode(FAN_OUT_PIN,    PWM);
    pinMode(AUX_OUT_PIN,    PWM);

    htimer1.setPrescaleFactor(1);
    htimer2.setPrescaleFactor(1);
    htimer3.setPrescaleFactor(1);
    htimer4.setPrescaleFactor(1);
    htimer1.setOverflow(2047);
    htimer2.setOverflow(2047); //32768-1
    htimer3.setOverflow(2047);
    htimer4.setOverflow(2047);

    setPolarity(STOP_OUT_PIN,   HIGH);
    setPolarity(BLIGHT_OUT_PIN, HIGH);
    setPolarity(FAN_OUT_PIN,    HIGH);
    setPolarity(AUX_OUT_PIN,    HIGH);

    pwmWrite(STOP_OUT_PIN,   STOP_HALF_VALUE);
    //pwmWrite(BLIGHT_OUT_PIN, 0);
    pwmWrite(FAN_OUT_PIN,    0);
    pwmWrite(AUX_OUT_PIN,    0);

    // Special functions
    pinMode(CAN_RX_PIN,    INPUT);
    pinMode(CAN_TX_PIN,    OUTPUT);
    adc_set_prescaler(ADC_PRE_PCLK2_DIV_2);
    //Serial3.begin(115200);

    // External interrupts
    attachInterrupt(CSFAULT_IN_PIN, csFaultCallback, FALLING);
    attachInterrupt(BLIGHT_IN_PIN,  callback,        CHANGE);
    attachInterrupt(HBEAM_IN_PIN,   callback,        CHANGE);
    attachInterrupt(LBEAM_IN_PIN,   callback,        CHANGE);
    attachInterrupt(LTURN_IN_PIN,   callback,        CHANGE);
    attachInterrupt(RTURN_IN_PIN,   callback,        CHANGE);
    attachInterrupt(WARN_IN_PIN,    callback,        CHANGE);
    attachInterrupt(HORN_IN_PIN,    callback,        CHANGE);
    attachInterrupt(BREAK_IN_PIN,   callback,        CHANGE);
    #if BOARD_VER != BOARD_VER_1_1
        attachInterrupt(AUX_IN_PIN,    callback, CHANGE);
    #endif

    // Clocks & system timer
    systick_init(SYSTICK); // 50 ms

    #if USE_ANALOG_STOP
//        rcc_clk_disable(RCC_ADC1);
    #endif
//    rcc_clk_disable(RCC_ADC2);
//    rcc_clk_disable(RCC_ADC3);
//    rcc_clk_disable(RCC_AFIO);
//    rcc_clk_disable(RCC_BKP);
//    rcc_clk_disable(RCC_CRC);
//    rcc_clk_disable(RCC_DAC);
//    rcc_clk_disable(RCC_DMA1);
//    rcc_clk_disable(RCC_DMA2);
//    rcc_clk_disable(RCC_FLITF);
//    rcc_clk_disable(RCC_FSMC);
//    rcc_clk_disable(RCC_I2C1);
//    rcc_clk_disable(RCC_I2C2);
//    rcc_clk_disable(RCC_SDIO);
//    rcc_clk_disable(RCC_SPI1);
//    rcc_clk_disable(RCC_SPI2);
//    rcc_clk_disable(RCC_SPI3);
//    rcc_clk_disable(RCC_TIMER1);
//    rcc_clk_disable(RCC_TIMER5);
//    rcc_clk_disable(RCC_TIMER6);
//    rcc_clk_disable(RCC_TIMER7);
//    rcc_clk_disable(RCC_TIMER8);
//    rcc_clk_disable(RCC_TIMER9);
//    rcc_clk_disable(RCC_TIMER10);
//    rcc_clk_disable(RCC_TIMER11);
//    rcc_clk_disable(RCC_TIMER12);
//    rcc_clk_disable(RCC_TIMER13);
//    rcc_clk_disable(RCC_TIMER14);
//    rcc_clk_disable(RCC_USART1);
//    rcc_clk_disable(RCC_USART2);
//    rcc_clk_disable(RCC_USART3);
//    rcc_clk_disable(RCC_UART4);
//    rcc_clk_disable(RCC_UART5);
    if (CAN_BUS_ENABLED) {
        rcc_clk_disable(RCC_CAN);
    }
}

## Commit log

2018-09-10 initial import
    [board.brd, board.sch]
2018-10-06 Schematics v1
    [board.brd, board.sch]
2018-10-06 PCB v.1
    [board.brd, board.sch]
2018-10-06 Board & schematics v 1.1. Minor improvements
    [board.brd, board.sch]
2018-10-15 Added BOM
    [board.brd, board.sch]
2019-03-10 Board v2, firmware is still WIP
    [board.brd, board.sch, board2.brd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]
2019-03-10 BOM for v2
    [board.brd, board.sch]
2019-03-10 minor v2 fixes
    [board.brd, board.sch]
2019-07-25 Updated v2 code, added 3d print models
    [Body.stl, Cover.stl, board.sch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]

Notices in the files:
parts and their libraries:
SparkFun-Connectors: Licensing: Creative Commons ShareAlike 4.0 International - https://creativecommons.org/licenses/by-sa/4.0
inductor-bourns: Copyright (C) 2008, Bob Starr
